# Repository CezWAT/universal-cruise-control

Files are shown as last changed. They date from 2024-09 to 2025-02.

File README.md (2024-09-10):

Universal cruise control for cars

# What it is
This project is about to bring cruise control to my Fiat 126p, but basically it should be possible to adapt it to any car.

# Sensors used
- hall sensor as a speed sensor
- brake light switch (already in place)
- clutch switch (has to be added)
- Three buttons (+, -, cancel)

# What is driving what
Based on the speed sensor, the device regulates PWM signal with PI loop. It tries to keep the vehicle speed as close as possible to the one set with the buttons. What controls the engine is a simple, but "strong" servomotor. In my case it is TiankongRC TD-6620MG (they say it has metal gears, 180 degrees of movement and 20 kg of torque). The servo is attached to gas pedal linkage as it is a simple connection and there are no vibrations on the floor compared to the engine.

# Where is the firmware
In FW directory. Be aware, that for now it is only a proof of concept made for HW v. 1. There are many functions that I would like to work but I didn't code it yet.

It's bare metal and I started writing it with HW v1, so I have to make some changes.

# Changes in HW between versions
v1:
- controls DC motor with H bridge. It came out as not so simple due to lack of motor position sensing.
- buttons and switches had to be debounced in code, this takes time and control over cruise control is somehow critical on the road.
- buttons were driven from the VCC.
- I misplaced pins in AMSR20783.3JZ footprint.

v2:
- improved misconceptions from above.
- JST connectors instead of goldpins.
- improved routing and footprints (for example SOT123 in place of SOT323 for improved solderability).

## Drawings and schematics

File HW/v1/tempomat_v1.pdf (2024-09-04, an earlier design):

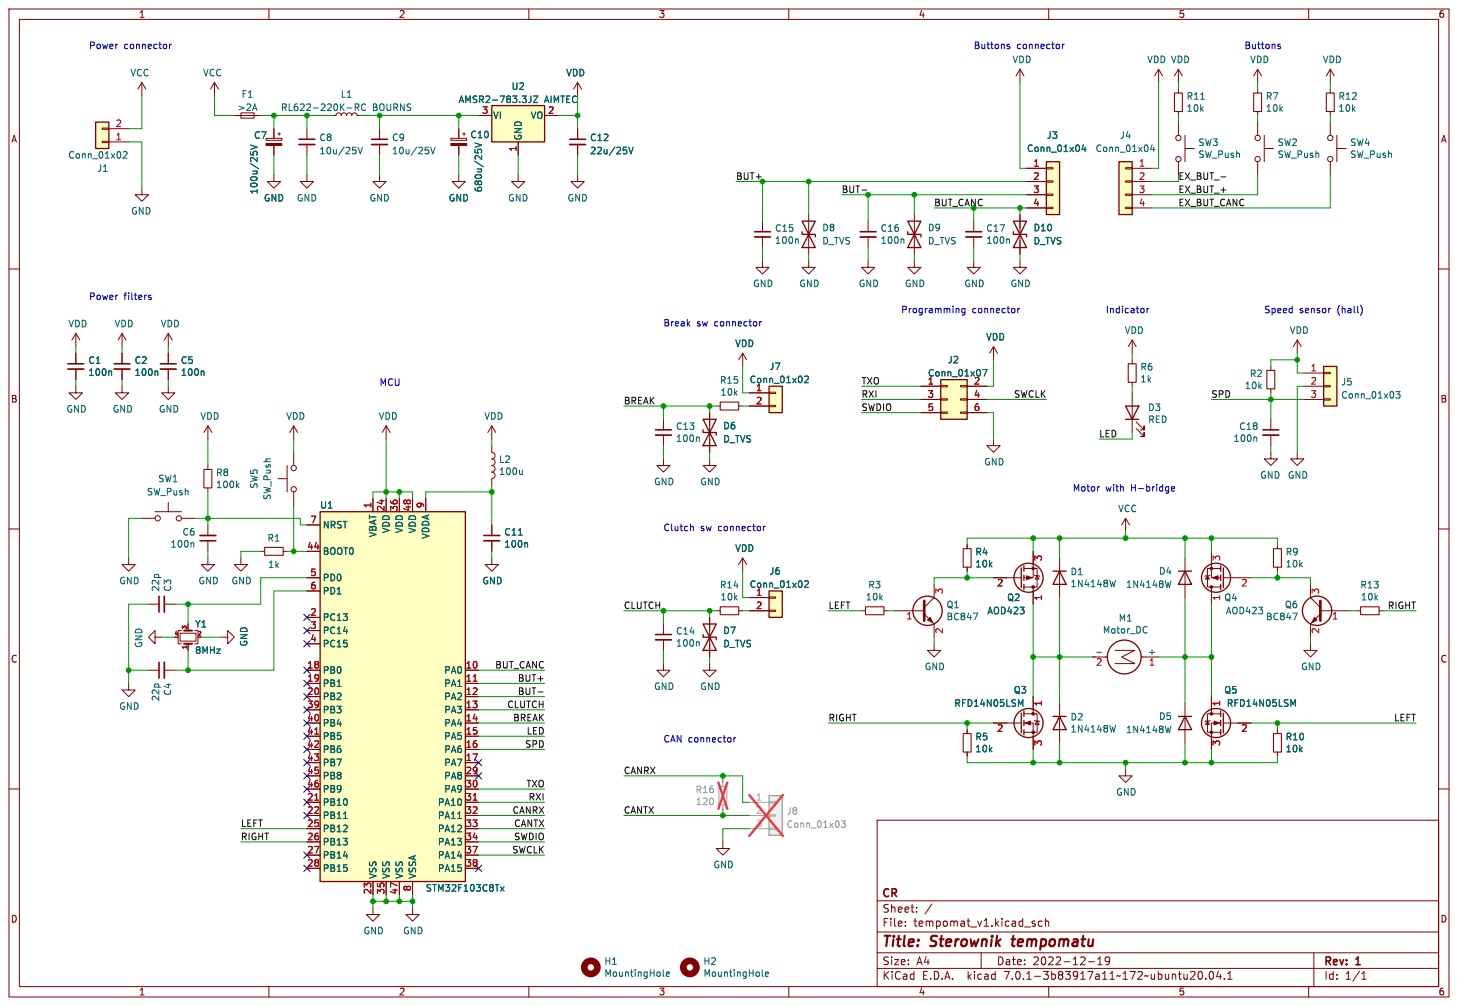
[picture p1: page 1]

1 PA0 10 PA1 11 PA2 12 PA3 13 PA4 14 PA5 15 PA6 16 PA7 17 PB0 18 PB1 19 PC13 2 PB2 20 PB10 21 PB11 22 VSS 23 VDD 24 PB12 25 PB13 26 PB14 27 PB15 28 PA8 29 PC14 3 PA9 30 PA10 31 PA11 32 PA12 33 PA13 34 VSS 35 VDD 36 PA14 37 PA15 38 PB3 39 PC15 4 PB4 40 PB5 41 PB6 42 PB7 43 BOOT0 44 PB8 45 PB9 46 VSS 47 VDD 48 PD0 5 PD1 6 NRST 7 VSSA

Id: 1/1 Title: Sterownik tempomatu

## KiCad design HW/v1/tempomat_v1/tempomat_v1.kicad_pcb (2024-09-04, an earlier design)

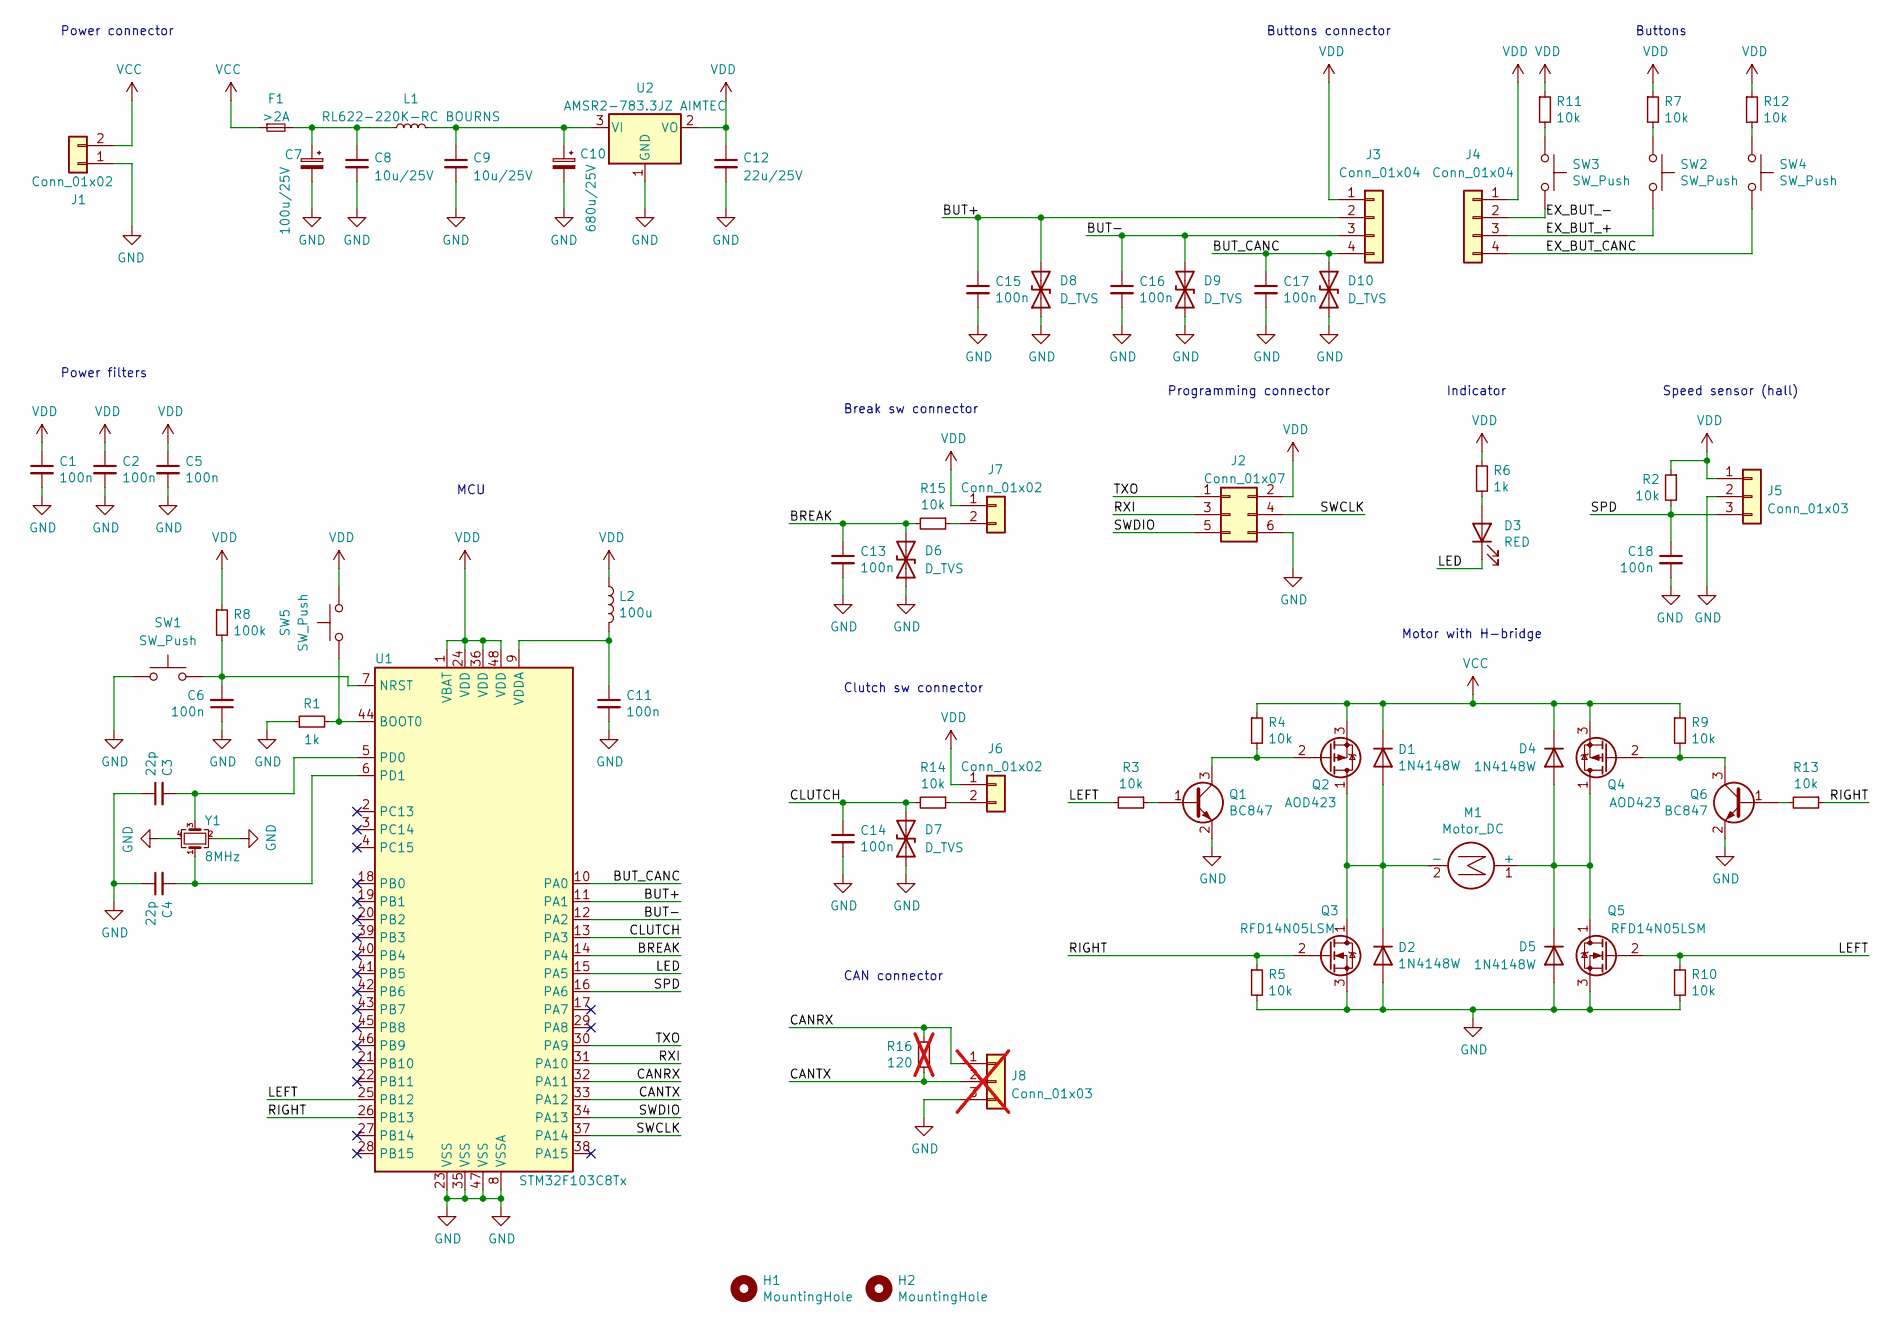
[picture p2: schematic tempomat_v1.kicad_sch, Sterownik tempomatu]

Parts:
C1, C2, C5, C6, C13, C14, C15, C16, C17, C18: 100n; C_0603_1608Metric
C3, C4: 22p; C_0603_1608Metric
C7: 100u/25V; CP_Radial_D5.0mm_P2.50mm
C8, C9: 10u/25V; C_1206_3216Metric
C10: 680u/25V; CP_Radial_D10.0mm_P5.00mm
C11: 100n; C_0603_1608Metric_Pad1.08x0.95mm_HandSolder
C12: 22u/25V; CP_Radial_D6.3mm_P2.50mm
D1, D2, D4, D5: 1N4148W; D_SOD-123
D3: RED; D_0603_1608Metric
D6, D7, D8, D9, D10: D_TVS; D_SOD-323_HandSoldering
F1: >2A; Fuse_0805_2012Metric
H1, H2: MountingHole; MountingHole_3.5mm
J1: Conn_01x02; TerminalBlock_bornier-2_P5.08mm
J2: Conn_01x07; PinHeader_2x03_P2.54mm_Vertical
J3, J4: Conn_01x04; PinHeader_1x04_P2.54mm_Vertical
J5: Conn_01x03; PinHeader_1x03_P2.54mm_Vertical
J6, J7: Conn_01x02; PinHeader_1x02_P2.54mm_Vertical
J8: Conn_01x03; PinHeader_1x03_P2.54mm_Vertical; not fitted
L1: RL622-220K-RC BOURNS; L_Radial_D8.7mm_P5.00mm_Fastron_07HCP
L2: 100u; L_1210_3225Metric_Pad1.42x2.65mm_HandSolder
M1: Motor_DC; PinHeader_1x02_P2.54mm_Vertical
Q1, Q6: BC847; SOT-23
Q2, Q4: AOD423; TO-252-3_TabPin1
Q3, Q5: RFD14N05LSM; TO-252-3_TabPin1
R1, R6: 1k; R_0603_1608Metric
R2, R3, R4, R5, R7, R9, R10, R11, R12, R13, R14, R15: 10k; R_0603_1608Metric
R8: 100k; R_0603_1608Metric
R16: 120; R_0603_1608Metric; not fitted
SW1, SW2, SW3, SW4, SW5: SW_Push; SW_PUSH_6mm
U1: STM32F103C8Tx; LQFP-48_7x7mm_P0.5mm
U2: AMSR2-783.3JZ AIMTEC; AMSR2-78JZ
Y1: 8MHz; Crystal_SMD_EuroQuartz_MJ-4Pin_5.0x3.2mm

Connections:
/BREAK: C13.1, D6.2 (A2), R15.2, U1.14 (PA4)
/BUT+: C15.1, D8.2 (A2), J3.2, U1.11 (PA1)
/BUT-: C16.1, D9.2 (A2), J3.3, U1.12 (PA2)
/BUT_CANC: C17.1, D10.2 (A2), J3.4, U1.10 (PA0)
/CANRX: J8.1, R16.1, U1.32 (PA11)
/CANTX: J8.2, R16.2, U1.33 (PA12)
/CLUTCH: C14.1, D7.2 (A2), R14.2, U1.13 (PA3)
/EX_BUT_+: J4.3, SW2.2
/EX_BUT_-: J4.2, SW3.2
/EX_BUT_CANC: J4.4, SW4.2
/LED: D3.1 (K), U1.15 (PA5)
/LEFT: Q5.2 (G), R3.2, R10.1, U1.25 (PB12)
/RIGHT: Q3.2 (G), R5.1, R13.1, U1.26 (PB13)
/RXI: J2.3, U1.31 (PA10)
/SPD: C18.1, J5.3, R2.2, U1.16 (PA6)
/SWCLK: J2.4, U1.37 (PA14)
/SWDIO: J2.5, U1.34 (PA13)
/TXO: J2.1, U1.30 (PA9)
GND: C1.2, C2.2, C3.1, C4.1, C5.2, C6.1, C7.2, C8.2, C9.2, C10.2, C11.2, C12.2, C13.2, C14.2, C15.2, C16.2, C17.2, C18.2, D2.2 (A), D5.2 (A), D6.1 (A1), D7.1 (A1), D8.1 (A1), D9.1 (A1), D10.1 (A1), J1.1, J2.6, J5.2, J8.3, Q1.2 (E), Q3.3 (S), Q5.3 (S), Q6.2 (E), R1.1, R5.2, R10.2, SW1.1, U1.8 (VSSA), U1.23 (VSS), U1.35 (VSS), U1.47 (VSS), U2.1 (GND), Y1.2, Y1.4
unnamed: C7.1, C8.1, F1.2, L1.1
unnamed: D1.2 (A), D2.1 (K), M1.2 (-), Q2.1 (D), Q3.1 (D)
unnamed: D3.2 (A), R6.2
unnamed: D4.2 (A), D5.1 (K), M1.1 (+), Q4.1 (D), Q5.1 (D)
unnamed: J6.2, R14.1
unnamed: J7.2, R15.1
unnamed: Q1.1 (B), R3.1
unnamed: Q1.3 (C), Q2.2 (G), R4.2
unnamed: Q4.2 (G), Q6.3 (C), R9.2
unnamed: Q6.1 (B), R13.2
unnamed: R7.2, SW2.1
unnamed: R11.2, SW3.1
unnamed: R12.2, SW4.1
unnamed: R1.2, SW5.2, U1.44 (BOOT0)
unnamed: C6.2, R8.2, SW1.2, U1.7 (NRST)
unnamed: C3.2, U1.5 (PD0), Y1.3
unnamed: C4.2, U1.6 (PD1), Y1.1
unnamed: C11.1, L2.2, U1.9 (VDDA)
unnamed: C9.1, C10.1, L1.2, U2.3 (VI)
VCC: D1.1 (K), D4.1 (K), F1.1, J1.2, Q2.3 (S), Q4.3 (S), R4.1, R9.1
VDD: C1.1, C2.1, C5.1, C12.1, J2.2, J3.1, J4.1, J5.1, J6.1, J7.1, L2.1, R2.1, R6.1, R7.1, R8.1, R11.1, R12.1, SW5.1, U1.1 (VBAT), U1.24 (VDD), U1.36 (VDD), U1.48 (VDD), U2.2 (VO)

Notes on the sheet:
Buttons
MCU
Programming connector
Buttons connector
Power connector
Clutch sw connector
Indicator
Power filters
Speed sensor (hall)
CAN connector
Break sw connector
Motor with H-bridge

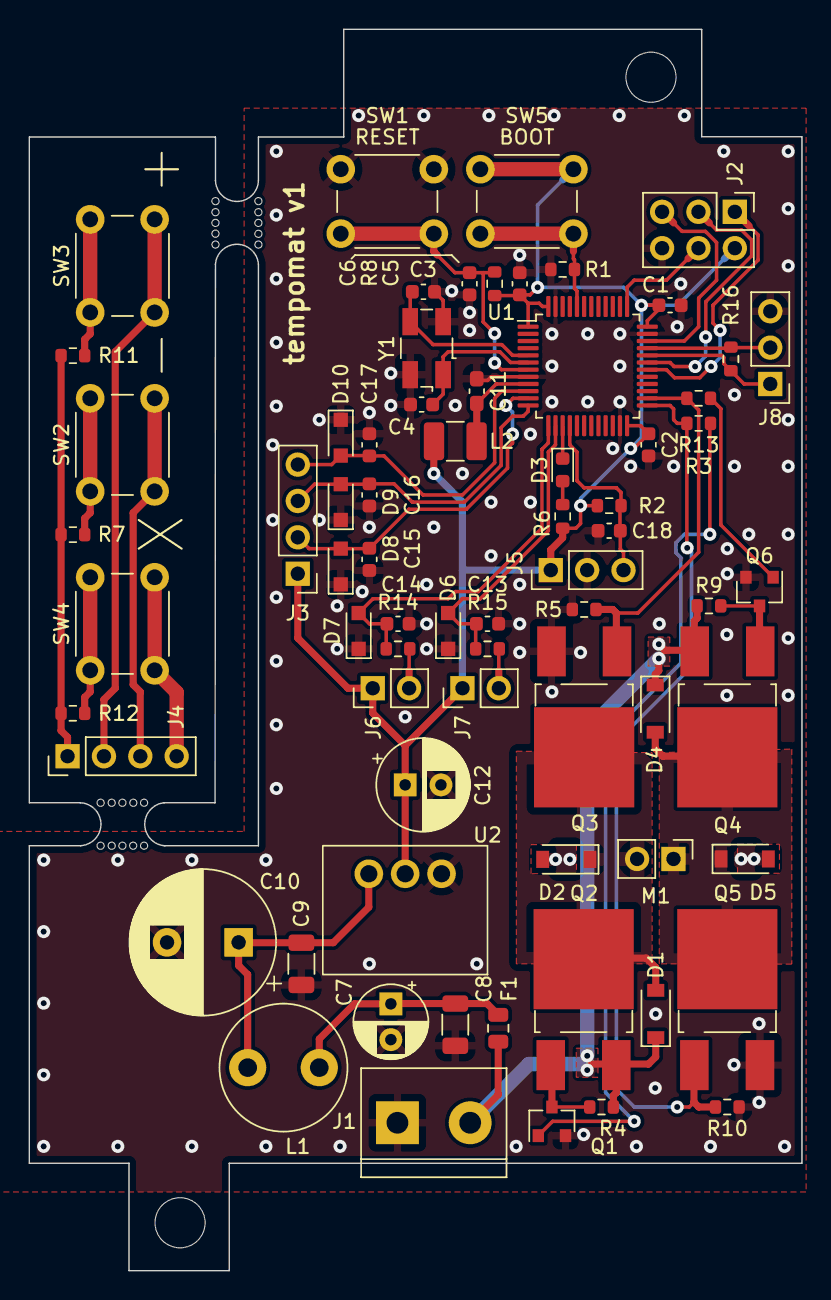
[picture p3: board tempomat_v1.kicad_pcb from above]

Board: 2 copper layers, 54.0 x 86.7 mm, 74 parts (0 on the bottom side), 40 nets.

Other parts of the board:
mouse-bite-3mm-slot, mouse-bite-3mm-slot#2: VAL**; mouse-bite-3mm-slot

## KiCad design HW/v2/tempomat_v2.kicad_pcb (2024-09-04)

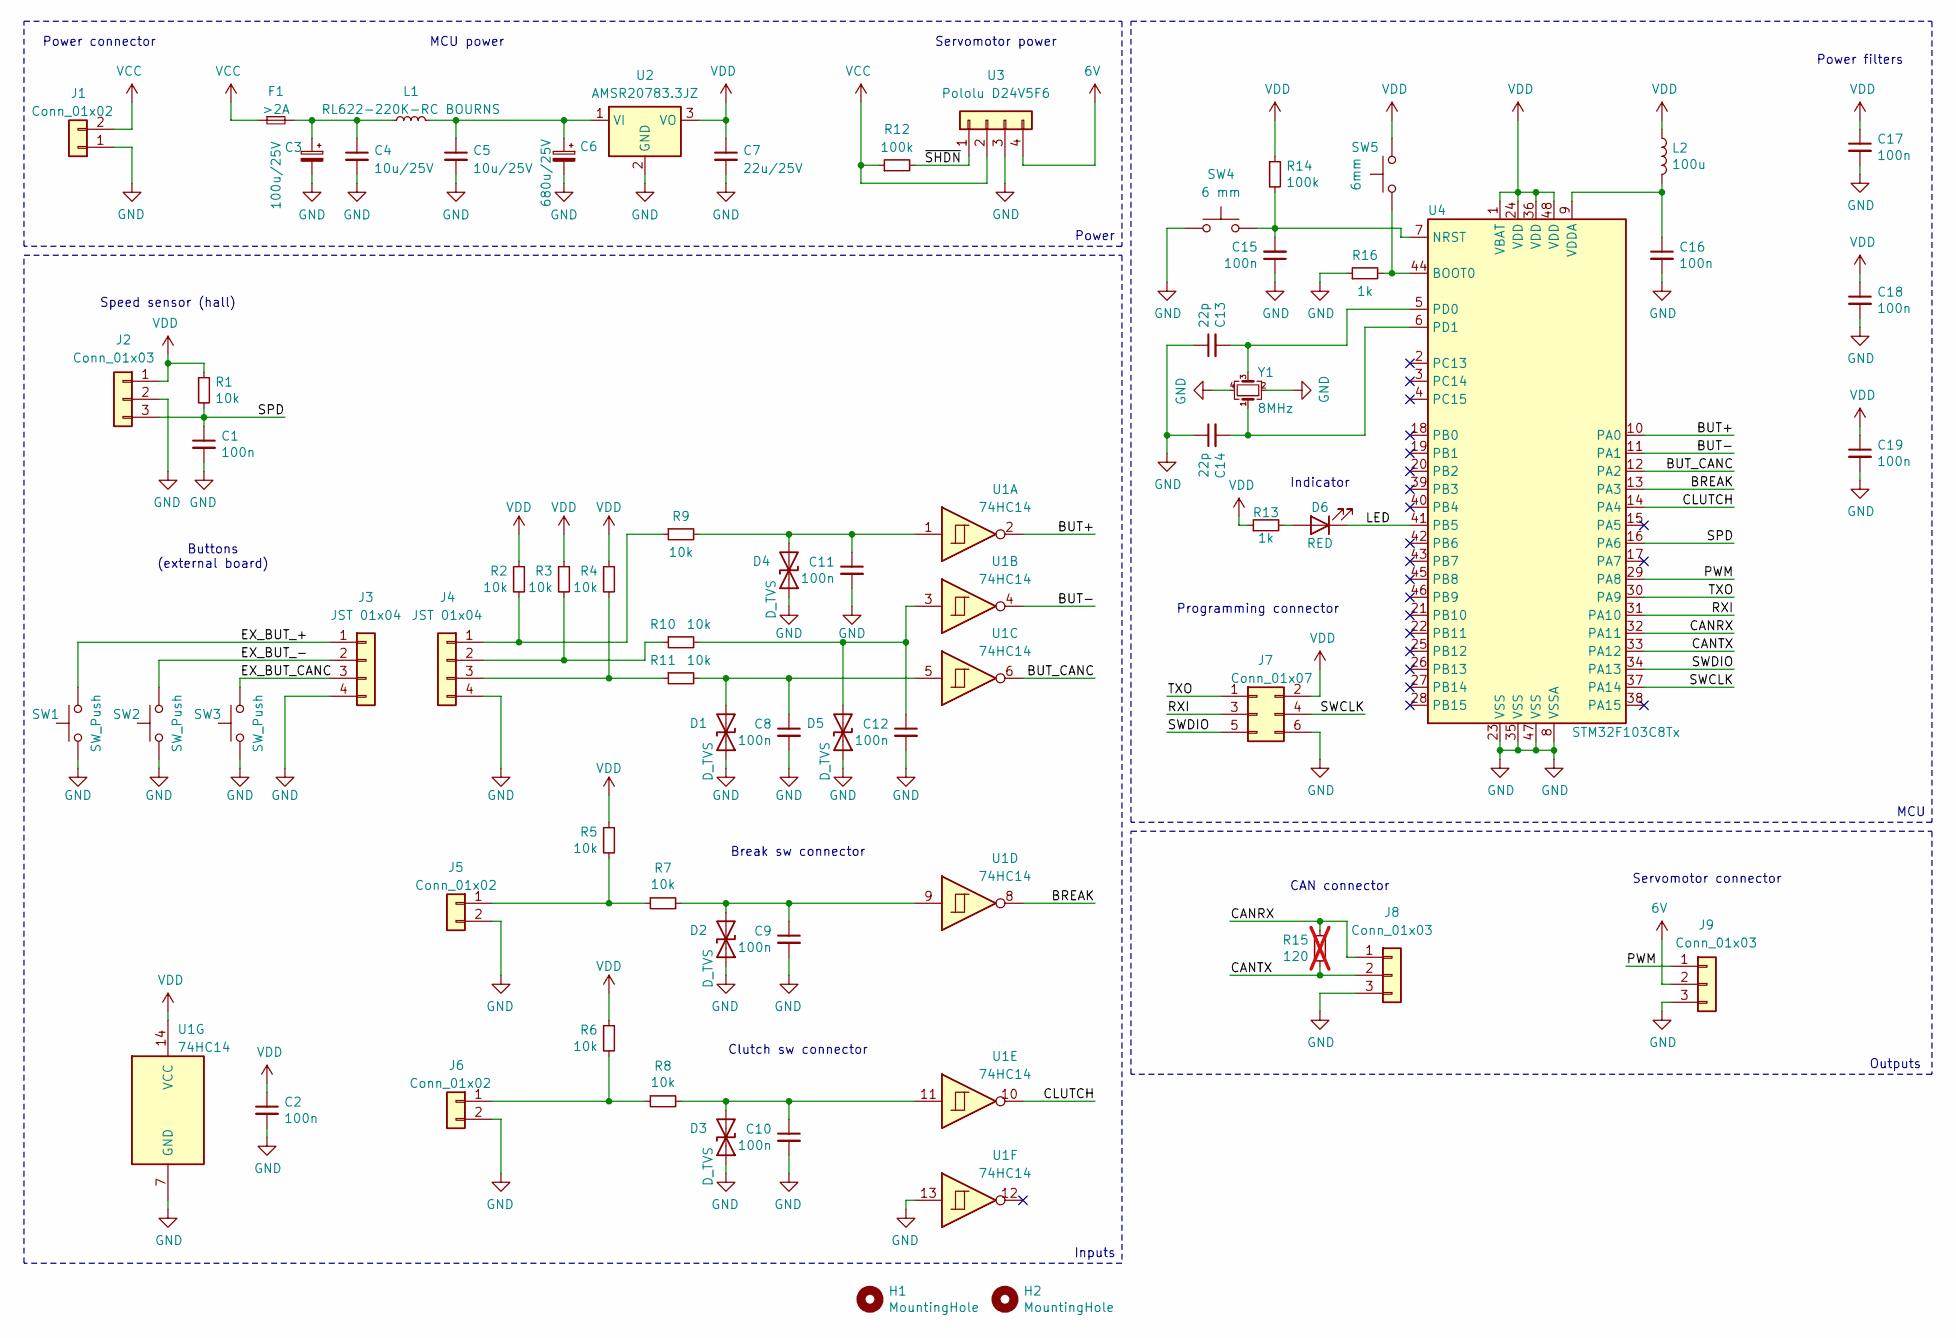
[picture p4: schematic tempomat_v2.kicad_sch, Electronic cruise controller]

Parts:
C1, C2, C8, C9, C10, C11, C12, C15, C17, C18, C19: 100n; C_0603_1608Metric
C3: 100u/25V; CP_Radial_D5.0mm_P2.50mm
C4, C5: 10u/25V; C_1206_3216Metric
C6: 680u/25V; CP_Radial_D10.0mm_P5.00mm
C7: 22u/25V; CP_Radial_D6.3mm_P2.50mm
C13, C14: 22p; C_0603_1608Metric
C16: 100n; C_0603_1608Metric_Pad1.08x0.95mm_HandSolder
D1, D2, D3, D4, D5: D_TVS; D_SOD-123
D6: RED; D_0603_1608Metric
F1: >2A; Fuse_0805_2012Metric
H1, H2: MountingHole; MountingHole_2.5mm
J1: Conn_01x02; TerminalBlock_bornier-2_P5.08mm
J2, J8, J9: Conn_01x03; JST_PH_B3B-PH-K_1x03_P2.00mm_Vertical
J3, J4: JST 01x04; JST_PH_B4B-PH-K_1x04_P2.00mm_Vertical
J5, J6: Conn_01x02; JST_PH_B2B-PH-K_1x02_P2.00mm_Vertical
J7: Conn_01x07; PinHeader_2x03_P2.54mm_Vertical
L1: RL622-220K-RC BOURNS; L_Radial_D8.7mm_P5.00mm_Fastron_07HCP
L2: 100u; L_1210_3225Metric_Pad1.42x2.65mm_HandSolder
R1, R2, R3, R4, R5, R6, R7, R8, R9, R10, R11: 10k; R_0603_1608Metric
R12, R14: 100k; R_0603_1608Metric
R13, R16: 1k; R_0603_1608Metric
R15: 120; R_0603_1608Metric; not fitted
SW1, SW2, SW3: SW_Push; SW_PUSH_6mm
SW4: 6 mm; SW_PUSH_6mm
SW5: 6mm; SW_PUSH_6mm
U1: 74HC14; SOIC-14_3.9x8.7mm_P1.27mm
U2: AMSR20783.3JZ; AMSR2-78JZ
U3: Pololu D24V5F6; PinHeader_1x04_P2.54mm_Vertical
U4: STM32F103C8Tx; LQFP-48_7x7mm_P0.5mm
Y1: 8MHz; Crystal_SMD_EuroQuartz_MJ-4Pin_5.0x3.2mm

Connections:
6V: J9.2, U3.4
/BREAK: U1.8, U4.13 (PA3)
/BUT+: U1.2, U4.10 (PA0)
/BUT-: U1.4, U4.11 (PA1)
/BUT_CANC: U1.6, U4.12 (PA2)
/CANRX: J8.1, R15.1, U4.32 (PA11)
/CANTX: J8.2, R15.2, U4.33 (PA12)
/CLUTCH: U1.10, U4.14 (PA4)
/EX_BUT_+: J3.1, SW1.2
/EX_BUT_-: J3.2, SW2.2
/EX_BUT_CANC: J3.3, SW3.2
/LED: D6.1 (K), U4.41 (PB5)
/PWM: J9.1, U4.29 (PA8)
/RXI: J7.3, U4.31 (PA10)
/SPD: C1.1, J2.3, R1.2, U4.16 (PA6)
/SWCLK: J7.4, U4.37 (PA14)
/SWDIO: J7.5, U4.34 (PA13)
/TXO: J7.1, U4.30 (PA9)
/~SHDN: R12.2, U3.1
GND: C1.2, C2.2, C3.2, C4.2, C5.2, C6.2, C7.2, C8.2, C9.2, C10.2, C11.2, C12.2, C13.1, C14.1, C15.1, C16.2, C17.2, C18.2, C19.2, D1.1 (A1), D2.1 (A1), D3.1 (A1), D4.1 (A1), D5.1 (A1), J1.1, J2.2, J3.4, J4.4, J5.2, J6.2, J7.6, J8.3, J9.3, R16.1, SW1.1, SW2.1, SW3.1, SW4.1, U1.7 (GND), U1.13, U2.2 (GND), U3.3, U4.8 (VSSA), U4.23 (VSS), U4.35 (VSS), U4.47 (VSS), Y1.2, Y1.4
unnamed: C3.1, C4.1, F1.2, L1.1
unnamed: C8.1, D1.2 (A2), R11.2, U1.5
unnamed: C9.1, D2.2 (A2), R7.2, U1.9
unnamed: C10.1, D3.2 (A2), R8.2, U1.11
unnamed: C11.1, D4.2 (A2), R9.2, U1.1
unnamed: C12.1, D5.2 (A2), R10.2, U1.3
unnamed: D6.2 (A), R13.2
unnamed: J4.1, R2.2, R9.1
unnamed: J4.2, R3.2, R10.1
unnamed: J4.3, R4.2, R11.1
unnamed: J5.1, R5.2, R7.1
unnamed: J6.1, R6.2, R8.1
unnamed: C5.1, C6.1, L1.2, U2.1 (VI)
unnamed: R16.2, SW5.2, U4.44 (BOOT0)
unnamed: C15.2, R14.2, SW4.2, U4.7 (NRST)
unnamed: C13.2, U4.5 (PD0), Y1.3
unnamed: C14.2, U4.6 (PD1), Y1.1
unnamed: C16.1, L2.2, U4.9 (VDDA)
VCC: F1.1, J1.2, R12.1, U3.2
VDD: C2.1, C7.1, C17.1, C18.1, C19.1, J2.1, J7.2, L2.1, R1.1, R2.1, R3.1, R4.1, R5.1, R6.1, R13.1, R14.1, SW5.1, U1.14 (VCC), U2.3 (VO), U4.1 (VBAT), U4.24 (VDD), U4.36 (VDD), U4.48 (VDD)

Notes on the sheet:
Inputs
Power
Buttons (external board)
Outputs
MCU
Programming connector
MCU power
Servomotor power
Servomotor connector
Power connector
Clutch sw connector
Indicator
Power filters
Speed sensor (hall)
CAN connector
Break sw connector

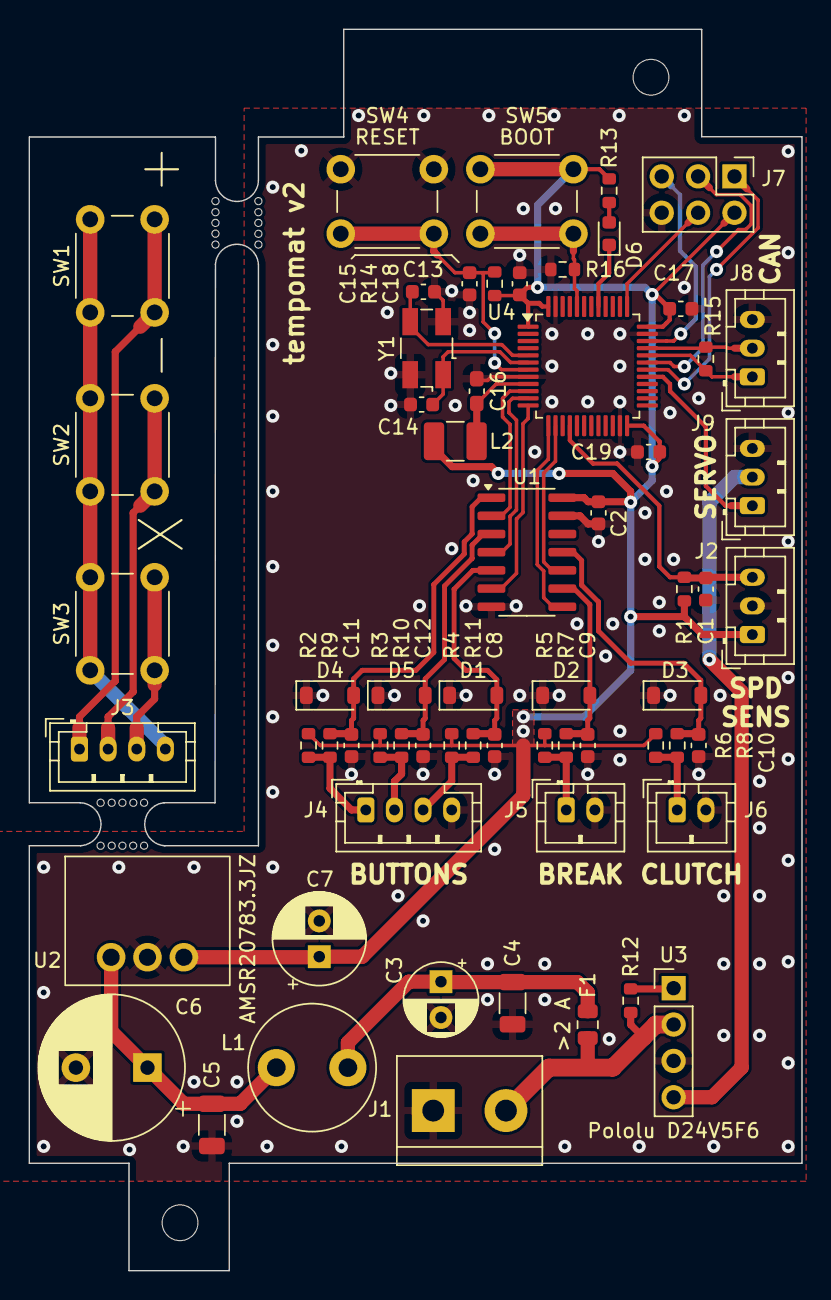
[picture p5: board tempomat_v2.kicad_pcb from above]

Board: 2 copper layers, 54.0 x 86.7 mm, 67 parts (0 on the bottom side), 40 nets.

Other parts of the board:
mouse-bite-3mm-slot, mouse-bite-3mm-slot#2: VAL**; mouse-bite-3mm-slot

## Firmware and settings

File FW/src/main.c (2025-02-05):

/*
Author      : CR
Version     : 1.0
Description : main file of cruise controller
MCU         : STM32F103C8
*/

// todo
/*
[v] "clean" start
	[V] sysclk
	[v] GPIO
	[v] timer for calculating speed
	[V] watchdog
	[V] uart
	[V] LED
	
[ ] PID
[v] speed reading
[ X ] read RPM
[?] PWM
[V] PLUS button working
[V] MINUS button working
[ ] CANCEL button working
[ ] clutch button working
[ ] break button working
[v] speed saved in RAM
[ ] "automatic" 50 km/h
[ ] setting throttle with el. motor
[ ] safety (RPM > max; button permanently pressed; speed measurement timeout)
*/

#include "stm32f10x.h"
#include "main.h"
#include "hal.h"
#include "timers.h"
#include "math.h"
#include "printf.h"


volatile uint32_t g_time_tick = LOOP_PERIOD_MS; // overflow for first start to happen right away
volatile uint32_t last_speed = 0;
volatile uint32_t target_speed = 0;
volatile uint8_t g_speed_ready;
volatile uint8_t click_count = 0;
volatile uint32_t last_click_time = 0;

int main(void)
{
	init();

	uint32_t watchdog_timeout = g_time_tick + WATCHDOG_TIMEOUT;
	uint32_t info_timeout = 0;
	uint32_t manage_buttons_timeout = 0;
	uint8_t cc_enabled = 0;
	uint32_t speed = 0;

	for (;;)
	{
		if (g_time_tick > watchdog_timeout)
		{
			watchdog_feed();
			watchdog_timeout = g_time_tick + WATCHDOG_TIMEOUT;
		}

		if (g_speed_ready == SPEED_READY)
		{
			uint32_t pwm_value = 0;
			speed = get_speed();

			// set servo/throttle
			if (target_speed >= MINIMUM_SPEED && target_speed <= MAXIMUM_SPEED  && cc_enabled && speed > 0)
			{
				pwm_value = calculate_pid(speed, target_speed);
				printf("target: %u speed: %u  pid %d\r\n", target_speed, speed, pwm_value); // debug	
				if (speed != target_speed)
				{
					set_motor(pwm_value);
				}
			}
			else if (!cc_enabled)
			{
				set_motor(PI_MIN); // disable cruise control
			}
		}

		if (g_time_tick > info_timeout)
		{
			GPIOA->ODR ^= (1 << 5);
			info_timeout = g_time_tick + INFO_LOOP;
		}

		// reaction to buttons
		if (g_time_tick > manage_buttons_timeout)
		{
// clutch & break switches
			if (gpio_read(BUT_CLUTCH) || gpio_read(BUT_BREAK))
			{
				set_motor(PI_MIN); // todo not working if there is no speed signal
				cc_enabled = FALSE;
				printf(" CLUTCH/BREAK \r\n");
			}
// cancel
			if (gpio_read(BUT_CANC))
			{
				set_motor(PI_MIN); // todo not working if there is no speed signal
				last_speed = target_speed;
				cc_enabled = FALSE;
				printf(" CANC \r\n");
			}
// plus
			if (multiclick_buttons(BUT_PLUS) == 1 && !cc_enabled)
			{
				target_speed = speed++;
				cc_enabled = TRUE;
				printf("++\r\n");
			}

			if (multiclick_buttons(BUT_PLUS) == 1 && cc_enabled)
			{
				target_speed++;
				// target speed clamping
				target_speed > MAXIMUM_SPEED ? target_speed = MAXIMUM_SPEED : FALSE;
				cc_enabled = TRUE;
				printf("++\r\n");
			}

			if (multiclick_buttons(BUT_PLUS) == 2)
			{
				target_speed = 50;
				printf(" set 50 \r\n");
			}
// minus
			if (gpio_read(BUT_MINUS) == 1 && !cc_enabled)
			{
				target_speed = last_speed;
				cc_enabled = TRUE;
				printf(" set last speed \r\n");
			}

			if (gpio_read(BUT_MINUS) == 1 && cc_enabled)
			{
				target_speed--;
				// target speed clamping
				target_speed < MINIMUM_SPEED ? target_speed = MINIMUM_SPEED : FALSE;
				printf("--\r\n");
			}
			manage_buttons_timeout = g_time_tick + BTN_MANAGE_TIMEOUT;
		}
	}
}

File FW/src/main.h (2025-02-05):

#ifndef MAIN_H
#define MAIN_H

// clock and prescalers
#define PCLK 8000000 // system clock from HSE
#define PRESCALE_PWM ((PCLK / (PCLK/100)) - 1) // counter
#define PRESCALE_TMR3 ((PCLK / (PCLK/100)) - 1) // counter
#define PRESCALE_TMR21 (PCLK / (PCLK/100))
#define SYSTICK_DELAY (PCLK / (PCLK/8000))

// timers config
#define LOOP_PERIOD_MS 3000 // main loop
#define WATCHDOG_TIMEOUT 5
#define INFO_LOOP 3000
#define BTN_LOOP 5
#define BTN_MANAGE_TIMEOUT 150

// HW values
#define ERROR_TR 3000 // critical error treshold value for ALARM
#define FLASH_PAGES 64
#define IWDG_EN 0xCCCC
#define IWDG_PRESCALER 1
#define IWDG_REFRESH 0xAAAA
#define UART_BAUD (PCLK/115200)
#define PULSE_FREQ 56 // @50 it was 44, compensated
#define PRESCALE_1MHZ 1000000
#define DOUBLE_CLICK_TIME 300 // in ms

enum speed_reading
{
	SPEED_NOT_READY,
	SPEED_WORKING,
	SPEED_READY
};

enum buttons
{
    BUT_CANC,
    BUT_PLUS,
    BUT_MINUS,
    BUT_CLUTCH,
    BUT_BREAK
};

// PI loop values
#define KP 20 // proportional gain
#define KI 25 // integral gain
#define PI_MAX 2390
#define PI_MIN 270
#define P_MAX 32767
#define I_MAX 32767

#define MINIMUM_SPEED 25
#define MAXIMUM_SPEED 145

#define TRUE 1
#define FALSE 0

#endif

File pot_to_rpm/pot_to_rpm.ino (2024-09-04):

/*
  Based on Analog Input Arduino example
  http://www.arduino.cc/en/Tutorial/AnalogInput
  
*/

int sensorPin = A0;    // select the input pin for the potentiometer
int ledPin = 2 ;      // select the pin for the LED
int sensorValue = 0;  // variable to store the value coming from the sensor

void setup() {
  // declare the ledPin as an OUTPUT:
  pinMode(ledPin, OUTPUT);
}

void loop() {
  digitalWrite(ledPin, HIGH);
  delay(map(analogRead(sensorPin), 0, 1023, 40, 200));
  digitalWrite(ledPin, LOW);
  delay(map(analogRead(sensorPin), 0, 1023, 40, 200));
}

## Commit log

2024-09-04 Add HW version 1 & 2
    [tempomat_v1.kicad_pcb, tempomat_v1.kicad_sch, tempomat_v2.kicad_pcb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]
2024-09-04 add license, add manual testing tool based on arduino
2025-02-05 Add double button press + button fixes
    [hal.c, main.c, main.h]
